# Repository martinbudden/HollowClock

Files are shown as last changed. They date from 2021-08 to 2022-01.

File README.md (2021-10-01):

# Hollow Clock

This **Hollow Clock** is a remix of the [Hollow clock 2 - silent and smooth](https://www.thingiverse.com/thing:4761858)
by [Shinsaku Hiura "shiura"](https://www.thingiverse.com/shiura/designs) and licensed under the same
Creative Commons - Attribution - Non-Commercial - Share Alike license [CC BY-NC-SA 4.0](https://creativecommons.org/licenses/by-nc-sa/4.0/).

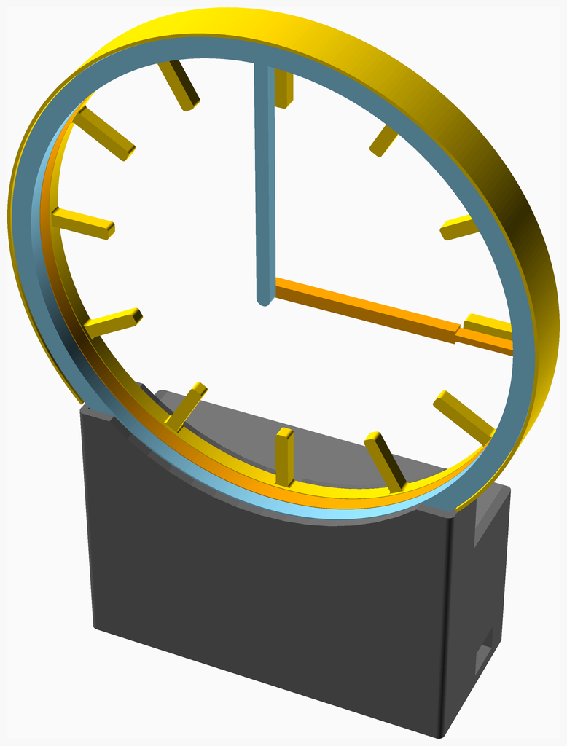
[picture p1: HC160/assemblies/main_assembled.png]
Main Assembly


## Assembly instructions

The assembly instructions and the BOM (parts list) are [here](HC160/readme.md).

The STL files are on [thingiverse](https://www.thingiverse.com/thing:4947971).

## Improvements to original design

I was having problems with the clock keeping time, mainly due to two reasons:

1. The gears sometimes skipped
2. The Arduino itself does not keep particularly good time

To solve these problems I made the following changes:

1. Changed the gearing to use involute gears
2. Added an axel to the reduction gear
3. Added a housing to the main clock face
4. Used a mortice and tenon joint to connect the clock face to the base
5. Recessed the gears to reduce friction
6. Used a Raspberry Pi Pico instead of an Arduino - this has a build in real time clock and so keeps much better time

Items 3 and 4 stop the clock face from "jumping" and skipping a tooth.

Additionally I changed the design of the base and cover, and the new cover can be printed without supports.

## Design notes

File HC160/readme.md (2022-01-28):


# HollowClock
# Hollow Clock Assembly Instructions

Main Assembly

<span></span>

---

## Table of Contents

1. [Parts list](#Parts_list)

1. [Clock Face Assembly](#Clock_Face_assembly)
1. [Gears Assembly](#Gears_assembly)
1. [Base Stage 1 Assembly](#Base_Stage_1_assembly)
1. [Base Assembly](#Base_assembly)
1. [Main Assembly](#main_assembly)

<span></span>
[Top](#TOP)

---

## Parts list

| <span style="writing-mode: vertical-rl; text-orientation: mixed;">Clock Face</span> | <span style="writing-mode: vertical-rl; text-orientation: mixed;">Gears</span> | <span style="writing-mode: vertical-rl; text-orientation: mixed;">Base</span> | <span style="writing-mode: vertical-rl; text-orientation: mixed;">Main</span> | <span style="writing-mode: vertical-rl; text-orientation: mixed;">TOTALS</span> |  |
|---:|---:|---:|---:|---:|:---|
|  |  |  |  | | **Vitamins** |
| &nbsp;&nbsp;.&nbsp; | &nbsp;&nbsp;.&nbsp; | &nbsp;&nbsp;4&nbsp; | &nbsp;&nbsp;.&nbsp; |  &nbsp;&nbsp;4&nbsp; | &nbsp;&nbsp; Bolt M2 caphead x  6mm |
| &nbsp;&nbsp;.&nbsp; | &nbsp;&nbsp;.&nbsp; | &nbsp;&nbsp;2&nbsp; | &nbsp;&nbsp;.&nbsp; |  &nbsp;&nbsp;2&nbsp; | &nbsp;&nbsp; Bolt M3 buttonhead x  6mm |
| &nbsp;&nbsp;.&nbsp; | &nbsp;&nbsp;.&nbsp; | &nbsp;&nbsp;3&nbsp; | &nbsp;&nbsp;2&nbsp; |  &nbsp;&nbsp;5&nbsp; | &nbsp;&nbsp; Bolt M3 buttonhead x  8mm |
| &nbsp;&nbsp;.&nbsp; | &nbsp;&nbsp;.&nbsp; | &nbsp;&nbsp;1&nbsp; | &nbsp;&nbsp;.&nbsp; |  &nbsp;&nbsp;1&nbsp; | &nbsp;&nbsp; Bolt M3 caphead x 16mm |
| &nbsp;&nbsp;.&nbsp; | &nbsp;&nbsp;1&nbsp; | &nbsp;&nbsp;.&nbsp; | &nbsp;&nbsp;.&nbsp; |  &nbsp;&nbsp;1&nbsp; | &nbsp;&nbsp; Geared stepper - 28BYJ-48 5V |
| &nbsp;&nbsp;.&nbsp; | &nbsp;&nbsp;.&nbsp; | &nbsp;&nbsp;1&nbsp; | &nbsp;&nbsp;.&nbsp; |  &nbsp;&nbsp;1&nbsp; | &nbsp;&nbsp; Raspberry Pi Pico |
| &nbsp;&nbsp;.&nbsp; | &nbsp;&nbsp;.&nbsp; | &nbsp;&nbsp;1&nbsp; | &nbsp;&nbsp;.&nbsp; |  &nbsp;&nbsp;1&nbsp; | &nbsp;&nbsp; ZC-A0591 ULN2003 driver PCB |
| &nbsp;&nbsp;.&nbsp; | &nbsp;&nbsp;1&nbsp; | &nbsp;&nbsp;12&nbsp; | &nbsp;&nbsp;2&nbsp; | &nbsp;&nbsp;15&nbsp; | &nbsp;&nbsp;Total vitamins count |
|  |  |  |  | | **3D printed parts** |
| &nbsp;&nbsp;.&nbsp; | &nbsp;&nbsp;.&nbsp; | &nbsp;&nbsp;1&nbsp; | &nbsp;&nbsp;.&nbsp; |  &nbsp;&nbsp;1&nbsp; | &nbsp;&nbsp;Base.stl |
| &nbsp;&nbsp;1&nbsp; | &nbsp;&nbsp;.&nbsp; | &nbsp;&nbsp;.&nbsp; | &nbsp;&nbsp;.&nbsp; |  &nbsp;&nbsp;1&nbsp; | &nbsp;&nbsp;Clock_Face.stl |
| &nbsp;&nbsp;.&nbsp; | &nbsp;&nbsp;.&nbsp; | &nbsp;&nbsp;.&nbsp; | &nbsp;&nbsp;1&nbsp; |  &nbsp;&nbsp;1&nbsp; | &nbsp;&nbsp;Cover.stl |
| &nbsp;&nbsp;.&nbsp; | &nbsp;&nbsp;1&nbsp; | &nbsp;&nbsp;.&nbsp; | &nbsp;&nbsp;.&nbsp; |  &nbsp;&nbsp;1&nbsp; | &nbsp;&nbsp;Drive_Gear.stl |
| &nbsp;&nbsp;.&nbsp; | &nbsp;&nbsp;1&nbsp; | &nbsp;&nbsp;.&nbsp; | &nbsp;&nbsp;.&nbsp; |  &nbsp;&nbsp;1&nbsp; | &nbsp;&nbsp;Hour_Gear.stl |
| &nbsp;&nbsp;1&nbsp; | &nbsp;&nbsp;.&nbsp; | &nbsp;&nbsp;.&nbsp; | &nbsp;&nbsp;.&nbsp; |  &nbsp;&nbsp;1&nbsp; | &nbsp;&nbsp;Hour_Hand.stl |
| &nbsp;&nbsp;1&nbsp; | &nbsp;&nbsp;.&nbsp; | &nbsp;&nbsp;.&nbsp; | &nbsp;&nbsp;.&nbsp; |  &nbsp;&nbsp;1&nbsp; | &nbsp;&nbsp;Minute_Hand.stl |
| &nbsp;&nbsp;.&nbsp; | &nbsp;&nbsp;.&nbsp; | &nbsp;&nbsp;1&nbsp; | &nbsp;&nbsp;.&nbsp; |  &nbsp;&nbsp;1&nbsp; | &nbsp;&nbsp;Reduction_Gear.stl |
| &nbsp;&nbsp;3&nbsp; | &nbsp;&nbsp;2&nbsp; | &nbsp;&nbsp;2&nbsp; | &nbsp;&nbsp;1&nbsp; | &nbsp;&nbsp;8&nbsp; | &nbsp;&nbsp;Total 3D printed parts count |

<span></span>
[Top](#TOP)

---

## Clock Face Assembly

### 3D Printed parts

| 1 x Clock_Face.stl | 1 x Hour_Hand.stl | 1 x Minute_Hand.stl |
|---|---|---|
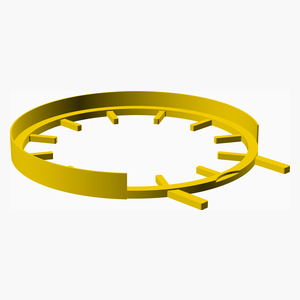
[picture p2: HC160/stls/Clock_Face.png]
Clock_Face.stl
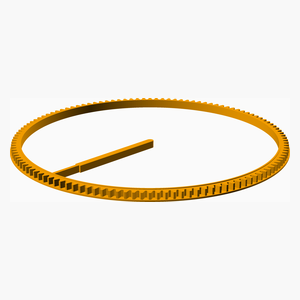
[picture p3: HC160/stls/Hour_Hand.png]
Hour_Hand.stl
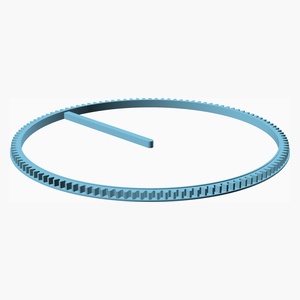
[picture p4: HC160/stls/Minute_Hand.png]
Minute_Hand.stl
|  |  |  

### Assembly instructions

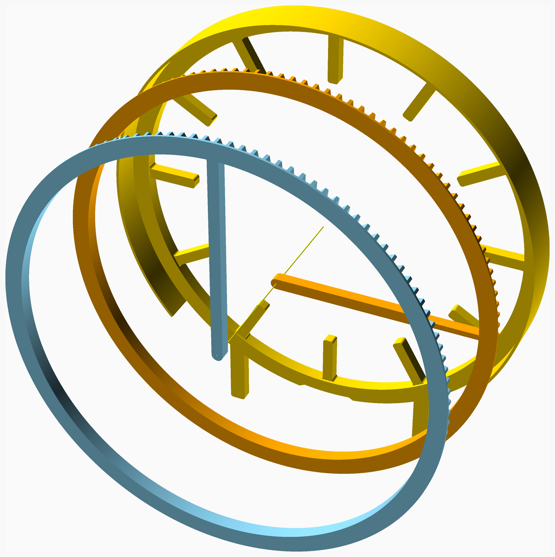
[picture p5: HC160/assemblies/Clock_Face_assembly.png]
Clock_Face_assembly


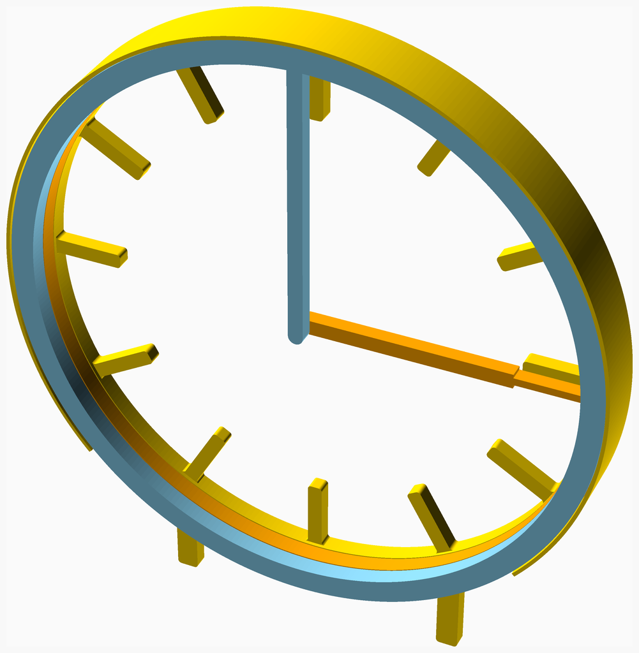
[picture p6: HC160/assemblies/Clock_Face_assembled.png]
Clock_Face_assembled


<span></span>
[Top](#TOP)

---

## Gears Assembly

### Vitamins

|Qty|Description|
|---:|:---|
|1| Geared stepper - 28BYJ-48 5V|

### 3D Printed parts

| 1 x Drive_Gear.stl | 1 x Hour_Gear.stl |
|---|---|
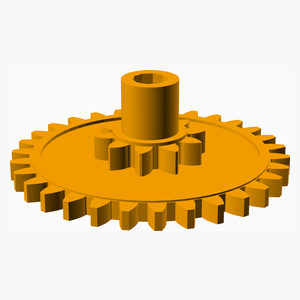
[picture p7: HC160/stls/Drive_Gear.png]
Drive_Gear.stl
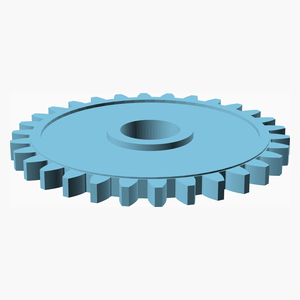
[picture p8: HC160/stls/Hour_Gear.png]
Hour_Gear.stl
|  |  

### Assembly instructions

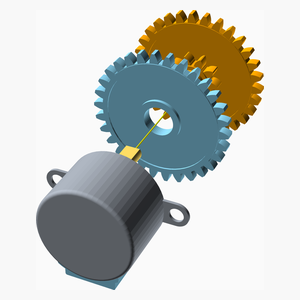
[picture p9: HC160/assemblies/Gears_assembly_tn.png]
Gears_assembly


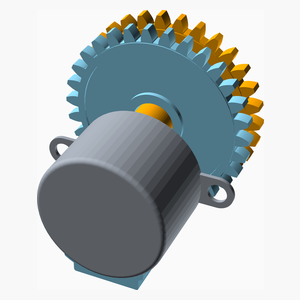
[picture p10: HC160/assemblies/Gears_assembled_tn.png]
Gears_assembled


<span></span>
[Top](#TOP)

---

## Base Stage 1 Assembly

### Vitamins

|Qty|Description|
|---:|:---|
|4| Bolt M2 caphead x  6mm|
|3| Bolt M3 buttonhead x  8mm|
|1| Bolt M3 caphead x 16mm|
|1| Raspberry Pi Pico|
|1| ZC-A0591 ULN2003 driver PCB|

### 3D Printed parts

| 1 x Base.stl | 1 x Reduction_Gear.stl |
|---|---|
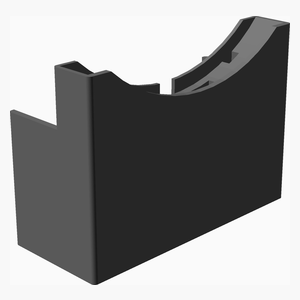
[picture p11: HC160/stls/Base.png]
Base.stl
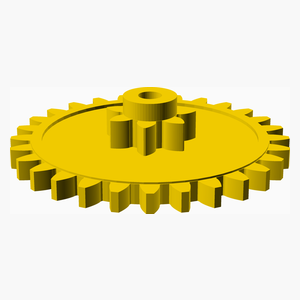
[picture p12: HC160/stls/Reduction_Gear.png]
Reduction_Gear.stl
|  |  

### Assembly instructions

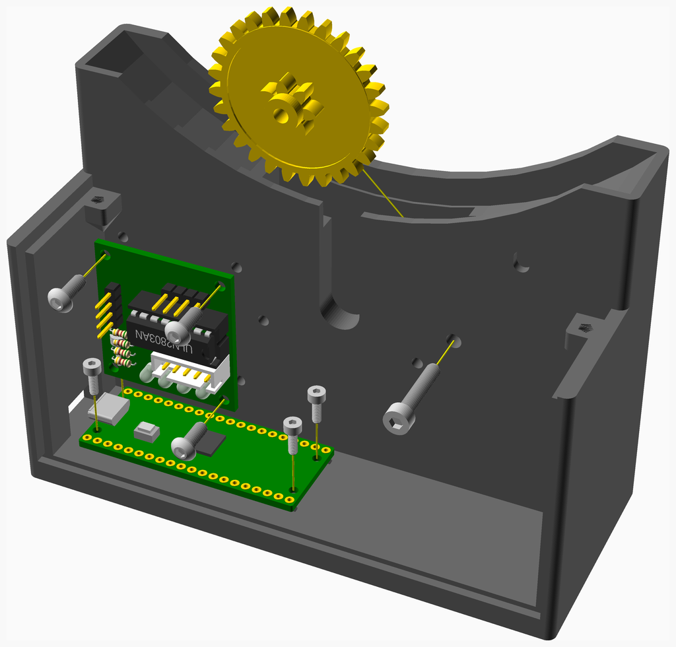
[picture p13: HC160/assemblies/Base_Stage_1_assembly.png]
Base_Stage_1_assembly


Wiring is easier if the stepper driver pcb is mounted "upside down" and attached with just 3 screws.

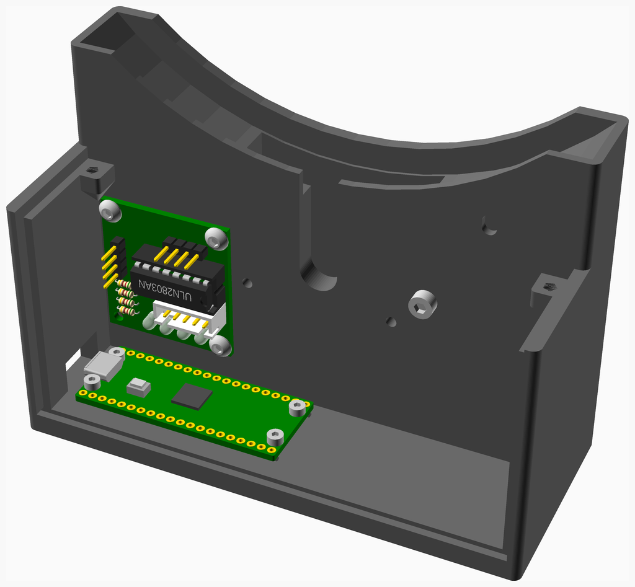
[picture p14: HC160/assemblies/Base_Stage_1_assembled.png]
Base_Stage_1_assembled


<span></span>
[Top](#TOP)

---

## Base Assembly

### Vitamins

|Qty|Description|
|---:|:---|
|2| Bolt M3 buttonhead x  6mm|

### Sub-assemblies

| 1 x Base_Stage_1_assembly | 1 x Gears_assembly |
|---|---|
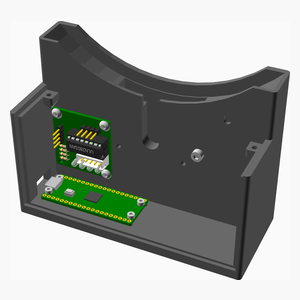
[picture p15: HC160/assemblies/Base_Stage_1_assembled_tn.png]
Base_Stage_1_assembled
|  | Gears_assembled 

### Assembly instructions

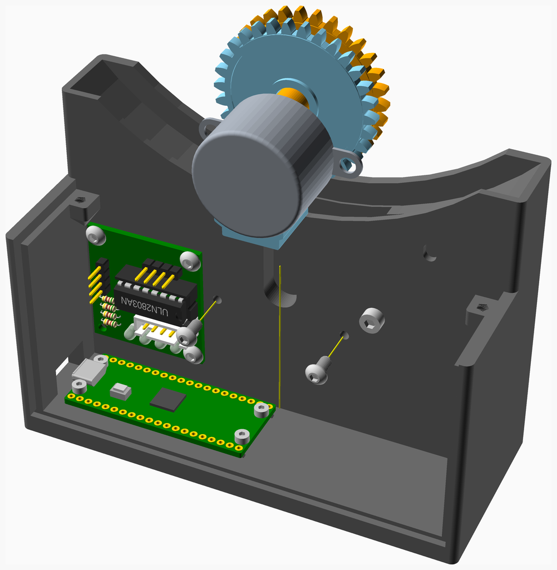
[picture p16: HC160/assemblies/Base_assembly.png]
Base_assembly


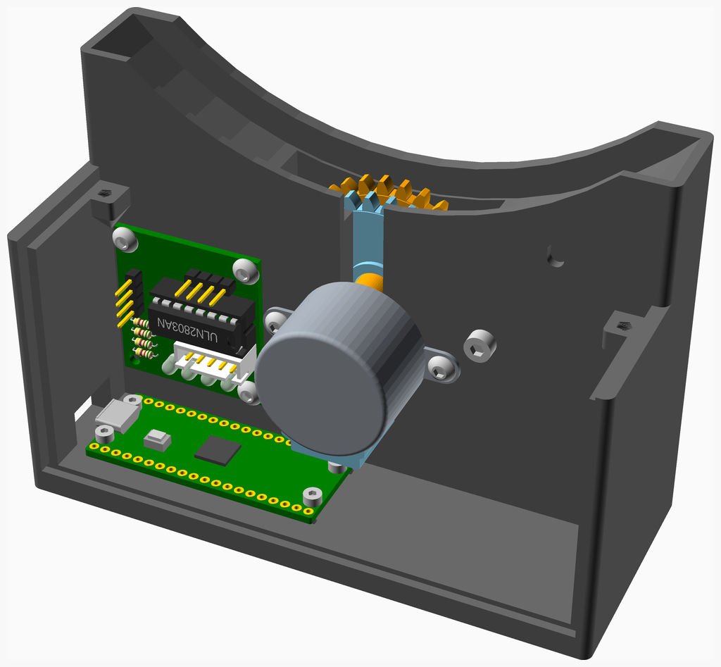
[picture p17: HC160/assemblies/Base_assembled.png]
Base_assembled


<span></span>
[Top](#TOP)

---

## Main Assembly

### Vitamins

|Qty|Description|
|---:|:---|
|2| Bolt M3 buttonhead x  8mm|

### 3D Printed parts

| 1 x Cover.stl |
|---|
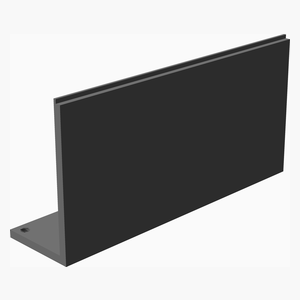
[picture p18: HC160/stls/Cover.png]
Cover.stl
|  

### Sub-assemblies

| 1 x Base_assembly | 1 x Clock_Face_assembly |
|---|---|
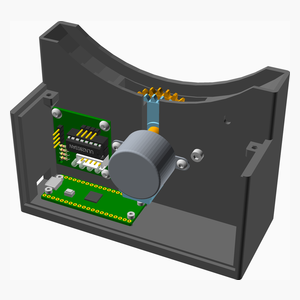
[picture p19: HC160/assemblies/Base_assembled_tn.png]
Base_assembled
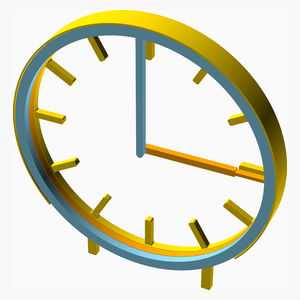
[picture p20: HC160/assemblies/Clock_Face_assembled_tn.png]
Clock_Face_assembled
|  |  

### Assembly instructions

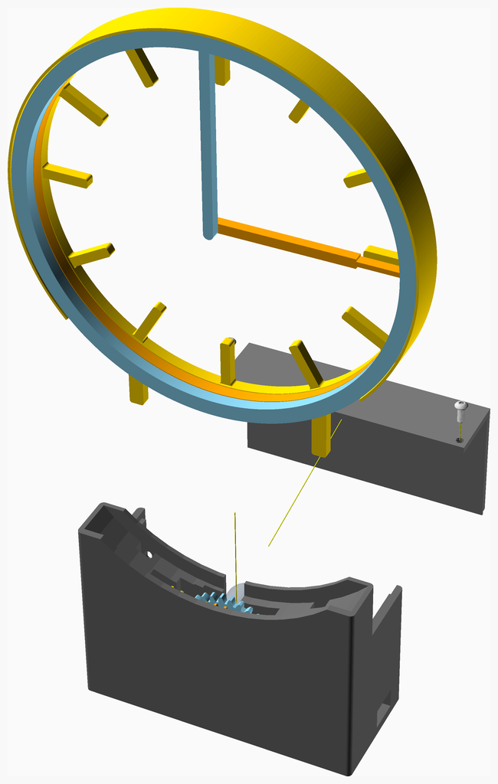
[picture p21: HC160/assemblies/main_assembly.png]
main_assembly


main_assembled

<span></span>
[Top](#TOP)

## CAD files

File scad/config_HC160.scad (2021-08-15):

_variant = "HC160";

_clockOD = 160;
_clockID = 147.5;
_clockFaceThickness = 5;

_baseSize = [120, 20, 60];
_footSize = [_baseSize.x, 30, 5];

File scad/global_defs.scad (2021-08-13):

$nozzle = 0.4;
$layer_height = 0.25;
$extrusion_width = 0.5;

$pp1_colour = "Gold";
$pp2_colour = "Orange";
$pp3_colour = "SkyBlue";
$pp4_colour = "DimGray";

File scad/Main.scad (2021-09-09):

//!# Hollow Clock Assembly Instructions
//!
//!
//!![Main Assembly](assemblies/main_assembled.png)
//!
//!
include <global_defs.scad>

include <NopSCADlib/core.scad>

include <target.scad>

use <printed/Base.scad>
use <printed/Clock.scad>

module main_assembly()
assembly("main") {
    rotate(180)
        Base_assembly();
    explode(100)
        Clock_Face_assembly();
    rotate(180)
        translate([0, -_footSize.y, _baseSize.z + 2*eps])
            explode([0, -100, 20], true) {
                hflip()
                    stl_colour(coverColor())
                        Cover_stl();
                Cover_hardware();
        }
}

if ($preview)
    main_assembly();

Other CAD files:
scad/printed/Base.scad
scad/printed/Clock.scad
tests/base.scad
tests/baseGears.scad
tests/clock.scad
tests/gears.scad

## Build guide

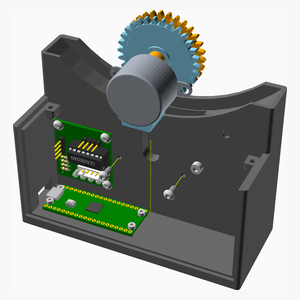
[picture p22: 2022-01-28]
HC160/assemblies/Base_assembly_tn.png

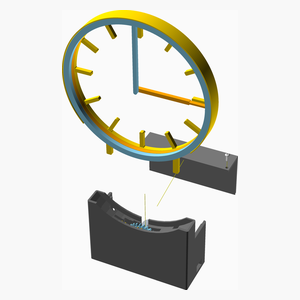
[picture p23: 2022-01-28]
HC160/assemblies/main_assembly_tn.png

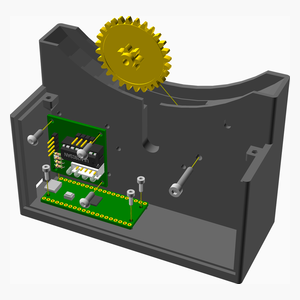
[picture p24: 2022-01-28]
HC160/assemblies/Base_Stage_1_assembly_tn.png

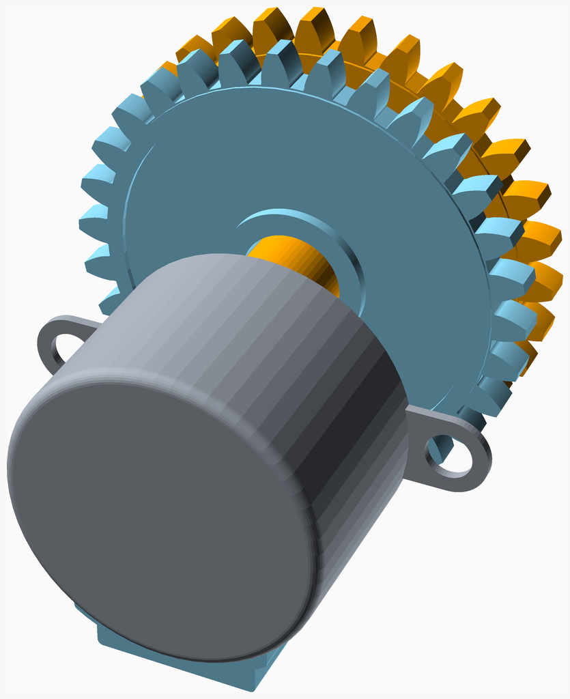
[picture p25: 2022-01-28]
HC160/assemblies/Gears_assembled.png

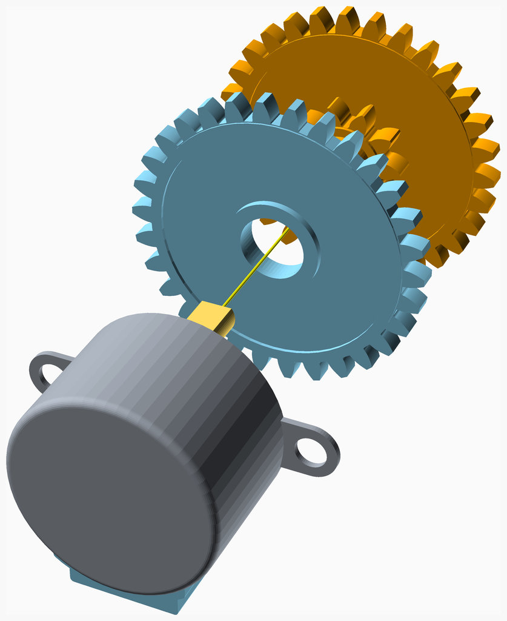
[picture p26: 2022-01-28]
HC160/assemblies/Gears_assembly.png

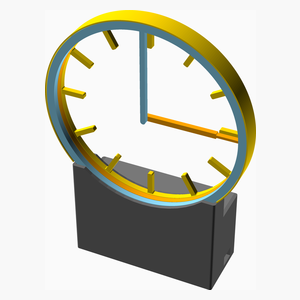
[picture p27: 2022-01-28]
HC160/assemblies/main_assembled_tn.png

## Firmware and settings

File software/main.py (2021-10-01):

from time import sleep
from machine import Pin
import utime
from micropython import const


class Stepper_Motor_28BYJ_48:
    """A 28BYJ-48 geared stepper motor."""

    # The 28BYJ-48 has 32 full steps per revolution (so 64 half-steps per revolution).
    # Gearing is 32/9 * 22/11 * 26/9 * 31/10 = 51584 / 810 = 25792 / 405 (= 63.68395 ~ 64).
    # So there are 32 * 25792 / 405 (=2037.8864 ~ 2038) full steps per revolution.
    # See https://lastminuteengineers.com/28byj48-stepper-motor-arduino-tutorial/
    STEPS_PER_REVOLUTION = const(32)
    GEAR_NUMERATOR = const(25792)
    GEAR_DENOMINATOR = const(405)
    GEARED_STEPS_PER_REVOLUTION = const(2048)

    # half step gives greater precision at the cost of less torque
    SWITCHING_SEQUENCE_HALF_STEP = (
        (1, 0, 0, 0),
        (1, 1, 0, 0),
        (0, 1, 0, 0),
        (0, 1, 1, 0),
        (0, 0, 1, 0),
        (0, 0, 1, 1),
        (0, 0, 0, 1),
        (1, 0, 0, 1),
    )

    # full step gives higher torque
    SWITCHING_SEQUENCE_FULL_STEP = (
        (1, 1, 0, 0),
        (0, 1, 1, 0),
        (0, 0, 1, 1),
        (1, 0, 0, 1),
    )

    def __init__(self, pins, led=None):
        self.pins = pins
        self.led = led
        self._switchingSequence = self.SWITCHING_SEQUENCE_FULL_STEP
        self._phaseCount = len(self._switchingSequence)
        self._phase = 0
        self.totalStepsRotated = 0
        self.timeBetweenStepsMs = 10  # minimum before skipping steps = 3ms
        self.led.value(0)
        for pin in self.pins:
            pin.value(0)

    def rotate(self, steps, debug=False):
        """Rotate the motor the given number of steps."""
        if debug:
            print("phase1=", self._phase)
        for _ in range(abs(steps)):
            if steps < 0:
                self._phase = (self._phase - 1) % self._phaseCount
            if debug:
                print("pins=", self._switchingSequence[self._phase])
            for i, pin in enumerate(self.pins):
                pin.value(self._switchingSequence[self._phase][i])
            if steps > 0:
                self._phase = (self._phase + 1) % self._phaseCount
            utime.sleep_ms(self.timeBetweenStepsMs)
            if self.led is not None:
                self.led.toggle()
        if self.led is not None:
            self.led.value(0)  # Pico led off
        if debug:
            print("phase2=", self._phase)
        self.totalStepsRotated += steps

    def powerOff(self):
        for pin in self.pins:
            pin.value(0)

    def revolutionsToSteps(self, revolutions):
        """Return the number of steps required for the number of revolutions specified."""
        # return revolutions * self.STEPS_PER_REVOLUTION * self.GEAR_NUMERATOR / self.GEAR_DENOMINATOR
        # calculated value is 2037.886
        # However this value gains time with the stepper motor I purchased, 2048 gives the correct time.
        return revolutions * self.GEARED_STEPS_PER_REVOLUTION


# The clock's minute hand is geared 1/4, so one revolution of the 28BYJ-48 is 15 minutes=  15*60 seconds.
# So one second is 1 / (15 * 60) revolutions.
def secondsToSteps(stepper, seconds):
    """Return the number of steps required to advance the clock the given number of seconds."""
    return stepper.revolutionsToSteps(seconds / (15 * 60))


def main():
    # pin assignment
    PIN_A = Pin(6, Pin.OUT)  # Pico GPIO6 connected to stepper control pin IN1
    PIN_B = Pin(7, Pin.OUT)  # Pico GPIO7 connected to stepper control pin IN2
    PIN_C = Pin(8, Pin.OUT)  # Pico GPIO8 connected to stepper control pin IN3
    PIN_D = Pin(9, Pin.OUT)  # Pico GPIO9 connected to stepper control pin IN4
    LED = Pin(25, Pin.OUT)  # Pico LED

    PINS = (PIN_A, PIN_B, PIN_C, PIN_D)  # pin order for clockwise rotation

    calibrate = False
    debug = False

    stepper = Stepper_Motor_28BYJ_48(PINS, LED)
    # The clock's minute hand is geared 1/4, so one revolution of the 28BYJ-48 is 15 minutes=  15*60 seconds.
    # So one second is 1 / (15 * 60) revolutions.
    secondsPerStepperRevolution = 15 * 60
    motorOffBetweenTicks = False
    sleep(1)  # allow Pico to initialise

    startTime = utime.time()
    tickIntervalSeconds = 10  # so hands are moved every 10 seconds
    totalStepsRotated = 0
    if debug:
        print("startTime=", startTime)
        print("s1=", stepper.revolutionsToSteps(1))
        # print("ss(60)=", secondsToSteps(stepper, 60))
        print("ss(60)=", stepper.revolutionsToSteps(60 / secondsPerStepperRevolution))

    if calibrate:
        # stepper.rotate(secondsToSteps(stepper, 3 * 3600))
        print("sc=", stepper.revolutionsToSteps(2 * 4))
        stepper.rotate(stepper.revolutionsToSteps(2 * 4))

    # rotate 10 steps at startup, so clock does not appear dead to user
    # initialRotate = 10
    # rotateMotor(initialRotate)
    # totalStepsRotated += initialRotate

    while True and calibrate == False:
        timeNow = utime.time()
        elapsedTime = timeNow - startTime
        # totalStepsRequired = secondsToSteps(stepper, elapsedTime)
        totalStepsRequired = stepper.revolutionsToSteps(elapsedTime / secondsPerStepperRevolution)
        stepsToRotate = int(totalStepsRequired - stepper.totalStepsRotated)
        if debug:
            print("elapsedTime={}, totalStepsRequired={}, totalStepsRotated={}, stepsToRotate={}".format(elapsedTime, totalStepsRequired, totalStepsRotated, stepsToRotate))
        stepper.rotate(stepsToRotate, debug)

        # Experimental feature to save power by switching off motor between ticks.
        # Unfortunately if anything binds during a tick then when power is turned off
        # it may spring back, thus loosing steps.
        if motorOffBetweenTicks:
            stepper.powerOff()

        toSleep = tickIntervalSeconds - (utime.time() - timeNow)
        if debug:
            print("toSleep=", toSleep)
        utime.sleep(toSleep)


if __name__ == "__main__":
    main()

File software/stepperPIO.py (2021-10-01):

from time import sleep
from machine import Pin, Timer
from rp2 import PIO, StateMachine, asm_pio
import utime
import micropython


class Stepper_Motor_28BYJ_48_PIO:
    """A 28BYJ-48 geared stepper motor driven by Raspberry Pi Pico PIO."""

    # The 28BYJ-48 has 32 full steps per revolution (so 64 half-steps per revolution).
    # Gearing is 32/9 * 22/11 * 26/9 * 31/10 = 51584 / 810 = 25792 / 405 (= 63.68395 ~ 64).
    # So there are 32 * 25792 / 405 (=2037.8864 ~ 2038) full steps per revolution.
    # See https://lastminuteengineers.com/28byj48-stepper-motor-arduino-tutorial/
    STEPS_PER_REVOLUTION = 32
    GEAR_NUMERATOR = 25792
    GEAR_DENOMINATOR = 405
    GEARED_STEPS_PER_REVOLUTION = 2048

    SWITCHING_SEQUENCE_FULL_STEP = (
        (0b0001, 0b0010, 0b0100, 0b1000),
        (0b0010, 0b0100, 0b1000, 0b0001),
        (0b0100, 0b1000, 0b0001, 0b0010),
        (0b1000, 0b0001, 0b0010, 0b0100),
    )

    def __init__(self, smId=0, basePin=25, tickIntervalMs=1000, gearing=1, debug=False):
        self.tickIntervalMs = tickIntervalMs
        self.gearing = gearing
        self.debug = debug
        self.sm = StateMachine(smId)
        # StateMachine.init(program, freq=- 1, *, in_base=None, out_base=None, set_base=None, jmp_pin=None, sideset_base=None, in_shiftdir=None, out_shiftdir=None, push_thresh=None, pull_thresh=None)
        # minimum freq is 1908
        self.sm.init(self.prog, freq=2000, out_base=Pin(basePin))
        self.sm.active(0)
        self.sm.irq(self.irqHandler)
        self.timer = Timer()
        self._startTime = 0
        self._totalStepsRotated = 0
        self._switchingSequence = self.SWITCHING_SEQUENCE_FULL_STEP
        self._phaseCount = len(self._switchingSequence)
        self._phase = 0

    # https://docs.micropython.org/en/latest/library/rp2.html#rp2.asm_pio
    @asm_pio(out_init=(PIO.OUT_LOW,) * 4, out_shiftdir=PIO.SHIFT_RIGHT)
    # pylint: disable=no-method-argument
    def prog():
        # pylint: disable=undefined-variable,expression-not-assigned
        pull()  # pull from TX FIFO into OSR (Output Shift Register)
        mov(x, osr)  # move stepCount into X register

        pull()
        mov(y, osr)  # move bitPattern to Y register

        jmp(not_x, "end")  # jump to end if X register (stepCount) is zero

        label("loop")
        jmp(not_osre, "step")  # jump to step if OSR not empty
        mov(osr, y)  # all bits have been shifted out, so reload OSR from Y register

        label("step")
        out(pins, 4)[26]  # shift out 4 bits from OSR to GPIO pins and delay 26 clock cycles, total looptime = (4 + 26)*0.5ms = 15ms

        jmp(x_dec, "loop")  # jump to loop if X register (stepCount) not zero, post decrement X register

        label("end")
        # set irq number 0 relative to state machine and don't wait.
        # Relative irq number is calclated by replacing the low two bits of the irq number with the low two bits of the sum irq_num + sm_id
        irq(rel(0))

    def irqHandler(self, sm):
        """Interrupt handler: queue another tick"""
        sm.active(0)  # Stop the state machine
        self.timer.init(mode=Timer.ONE_SHOT, period=self.tickIntervalMs, callback=self.tick)

    def tick(self):
        """IRQ callback: update elapsedTime and rotate motor"""
        elapsedTime = utime.time() - self._startTime
        totalStepsRequired = self.revolutionsToSteps(elapsedTime) * self.gearing
        stepsToRotate = int(totalStepsRequired - self._totalStepsRotated)
        if self.debug:
            print("elapsedTime={}, totalStepsRequired={}, totalStepsRotated={}, stepsToRotate={}".format(elapsedTime, totalStepsRequired, self._totalStepsRotated, stepsToRotate))
        if not self.debug or self._totalStepsRotated < 50:
            self.rotate(stepsToRotate)

    def resetTime(self):
        self._startTime = utime.time()
        self._totalStepsRotated = 0

    def rotate(self, stepCount):
        """Rotate the motor the given number of steps."""
        if self.debug:
            print("phase=", self._phase)
        patterns = self._switchingSequence[self._phase]
        pattern = patterns[0] | (patterns[1] << 4) | (patterns[2] << 8) | (patterns[3] << 12)
        pattern |= pattern << 16
        self.sm.put(stepCount)  # Push stepCount onto the TX FIFO
        self.sm.put(pattern)  # Push stepCount onto TX FIFO
        self.sm.active(1)  # Start the state machine
        self._totalStepsRotated += stepCount
        self._phase = (self._phase + stepCount) % self._phaseCount

    def revolutionsToSteps(self, revolutions):
        """Return the number of steps required for the number of revolutions specified."""
        # return revolutions * self.STEPS_PER_REVOLUTION * self.GEAR_NUMERATOR / self.GEAR_DENOMINATOR
        return revolutions * self.GEARED_STEPS_PER_REVOLUTION


def main():
    micropython.alloc_emergency_exception_buf(100)
    stepper = Stepper_Motor_28BYJ_48_PIO(smId=0, basePin=25, tickIntervalMs=2000, gearing=1 / (15 * 60), debug=False)
    sleep(1)  # allow Pico to initialise
    stepper.resetTime()
    stepper.rotate(1)


if __name__ == "__main__":
    main()

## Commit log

2021-08-13 Initial submission.
    [Base.scad, Clock.scad, Main.scad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]
2021-08-15 Modified gears profile to reduce friction.
    [Clock.scad]
2021-08-15 Increased gear clearance. Added axel for idler gear.
    [Base.scad]
2021-08-15 Tests update.
    [base.scad, baseGears.scad, clock.scad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]
2021-08-15 Config update.
    [config_HC160.scad]
2021-08-15 Added drive gear with hex cutout for testing.
    [Clock.scad]
2021-08-15 Test update.
    [baseGears.scad]
2021-08-15 Refined gears.
    [Clock.scad]
2021-08-15 Improvements to bse.
    [Base.scad]
2021-08-16 Increase lug size.
    [Base.scad]
2021-08-16 Changed stepper motor into a class.
2021-08-16 Implemented cover. Added extraY to base.
    [Base.scad]
2021-08-16 Added boss to hour gear.
    [Clock.scad]
2021-08-16 Moved power saving into main.
2021-08-20 Code tidy and added calibration.
2021-08-20 Initial commit of stepperPIO.py.
2021-08-20 Moved all functions into stepper motor class.
2021-09-08 Updated assemblies.
    [Base.scad, Clock.scad, Main.scad]
2021-09-08 Rotated main assembly.
    [Main.scad]
2021-09-09 Part renaming and added transparency for tests.
    [Base.scad, Clock.scad, Main.scad]
2021-09-11 Improved clock face positioning. Enlarged cover lugs. Code tidy.
    [Base.scad, Clock.scad]
2021-10-01 Increaded bossHeight on driveGear to 0.5.
    [Clock.scad]
2021-10-01 Added readme and assembly instructions.
2021-10-17 Rotated stepper driver pcb for easier wiring.
    [Base.scad]
2022-01-28 Reduced clockHandRingThickness.
    [Clock.scad]
